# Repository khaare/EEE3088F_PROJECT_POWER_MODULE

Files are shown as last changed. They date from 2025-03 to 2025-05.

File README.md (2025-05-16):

# EEE3088F_PROJECT_POWER_MODULE
The project involves designing and manufacturing the Micromouse(MM) power module.
This repo has two more branches. One for Khaarendiwe and the other for Joshua.
These branches were separated because we worked on different parts of the design, focusing on
different requirements and specifications.

The final design schematic and PCB are under the Main PCB folder, and the folder submitted for manufacturing is the Submission #1 folder

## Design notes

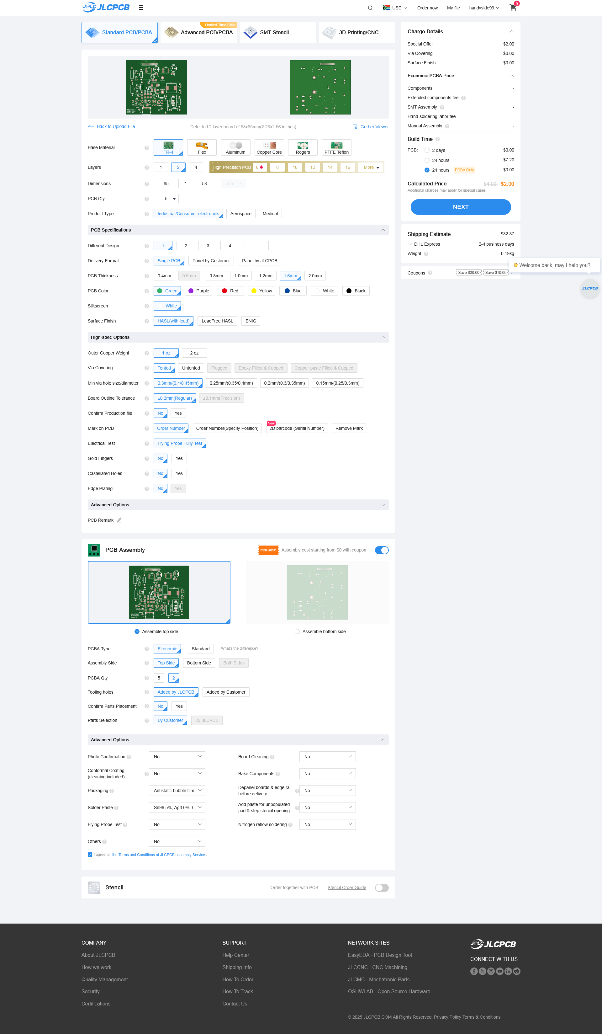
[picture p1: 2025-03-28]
Submission #1/EEE3088F 2025 Project PCB Files Group 46 HNDJOS012 MLDKHA010/EEE3088F_Project_JLCPCBacceptance_HNDJOS012.png

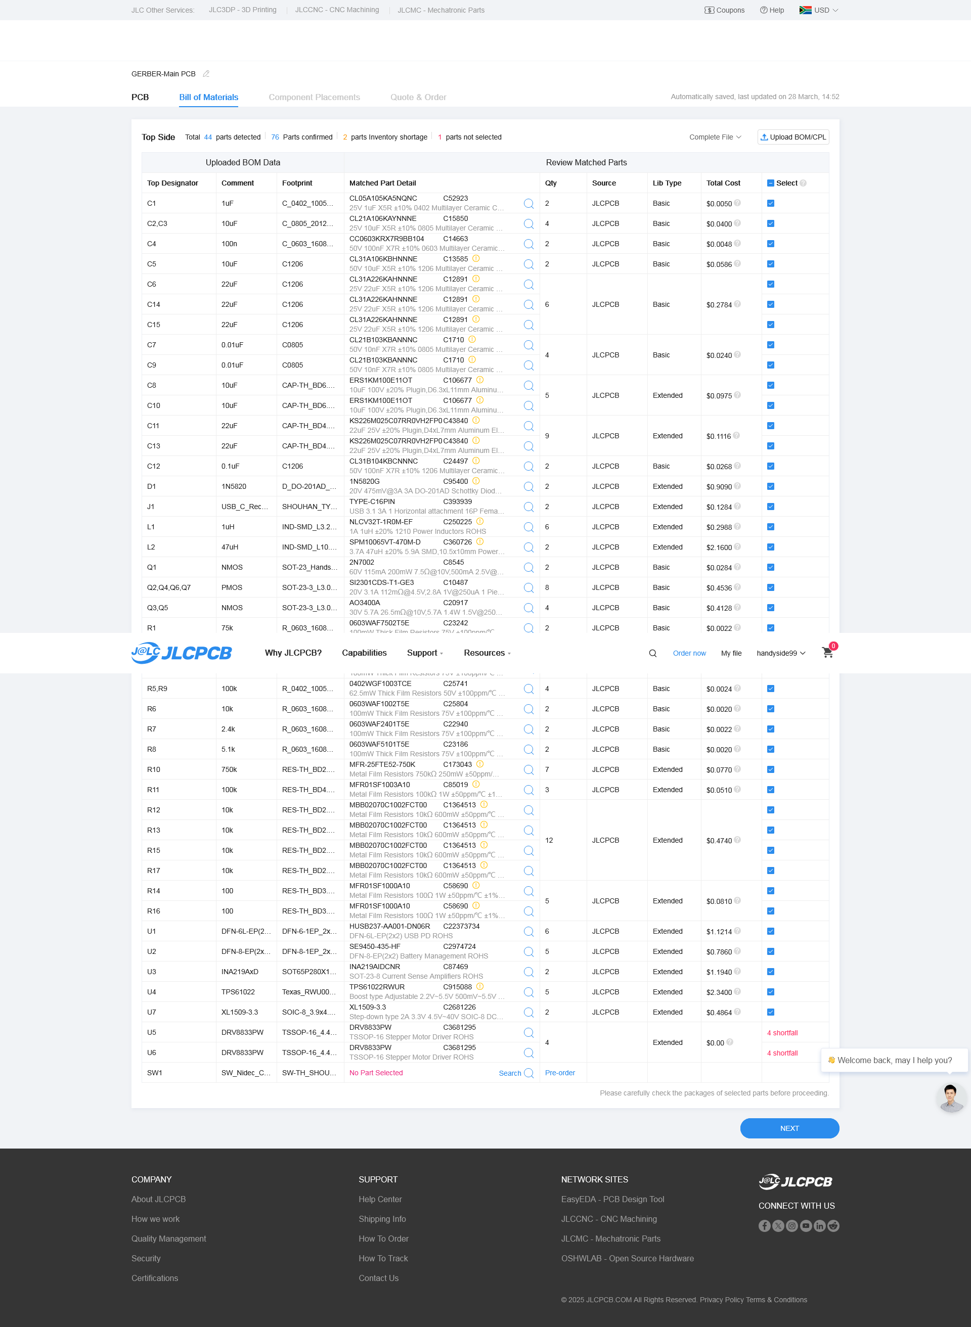
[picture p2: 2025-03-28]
Submission #1/EEE3088F 2025 Project PCB Files Group 46 HNDJOS012 MLDKHA010/EEE3088F_Project_JLCPCBBOM_HNDJOS012.png

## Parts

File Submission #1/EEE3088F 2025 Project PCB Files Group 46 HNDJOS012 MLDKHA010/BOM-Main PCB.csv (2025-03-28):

Comment | Designator | Footprint | LCSC | Quantity
PMOS | Q2,Q4,Q6,Q7 | SOT-23-3_L3.0-W1.7-P0.95-LS2.9-BR | C10487 | 4
100n | C4 | C_0603_1608Metric_Pad1.08x0.95mm_HandSolder | C14663 | 1
10uF | C2,C3 | C_0805_2012Metric_Pad1.18x1.45mm_HandSolder | C15850 | 2
NMOS | Q3,Q5 | SOT-23-3_L3.0-W1.7-P0.95-LS2.9-BR | C20917 | 2
DFN-6L-EP(2x2)_USB_PD_ROHS | U1 | DFN-6-1EP_2x2mm_P0.65mm_EP1x1.6mm | C22373734 | 1
2.4k | R7 | R_0603_1608Metric_Pad0.98x0.95mm_HandSolder | C22940 | 1
3.3k | R4 | R_0603_1608Metric_Pad0.98x0.95mm_HandSolder | C22978 | 1
5.1k | R8 | R_0603_1608Metric_Pad0.98x0.95mm_HandSolder | C23186 | 1
75k | R1 | R_0603_1608Metric_Pad0.98x0.95mm_HandSolder | C23242 | 1
100m | R2,R3 | R_1206_3216Metric_Pad1.30x1.75mm_HandSolder | C25334 | 2
100k | R5,R9 | R_0402_1005Metric_Pad0.72x0.64mm_HandSolder | C25741 | 2
10k | R6 | R_0603_1608Metric_Pad0.98x0.95mm_HandSolder | C25804 | 1
DFN-8-EP(2x2) Battery Management ROHS | U2 | DFN-8-1EP_2x2mm_P0.5mm_EP1.05x1.75mm | C2974724 | 1
USB_C_Receptacle_USB2.0_16P | J1 | SHOUHAN_TYPE-C_16PIN_2MD__073_ | C393939 | 1
1uF | C1 | C_0402_1005Metric_Pad0.74x0.62mm_HandSolder | C52923 | 1
NMOS | Q1 | SOT-23_Handsoldering | C8545 | 1
INA219AxD | U3 | SOT65P280X145-8N | C87469 | 1
0.01uF | C7 | C0805 |  | 1
SW_Nidec_CAS-120A1 | SW1 | SW-TH_SHOU-HAN_SS12D10G4 |  | 1
XL1509-3.3 | U7 | SOIC-8_3.9x4.9mm_P1.27mm |  | 1
22uF | C14 | C1206 |  | 1
TPS61022 | U4 | Texas_RWU0007A_VQFN-7_2x2mm_P0.5mm |  | 1
Conn_01x02_Pin | J3 | PinHeader_1x02_P1.00mm_Vertical |  | 1
10uF | C10 | CAP-TH_BD6.3-P2.50-D1.0-FD |  | 1
22uF | C13 | CAP-TH_BD4.0-P1.50-D0.8-FD |  | 1
22uF | C6 | C1206 |  | 1
1uH | L1 | IND-SMD_L3.2-W2.5_L3225 |  | 1
100k | R11 | RES-TH_BD4.0-L11.5-P15.50-D0.7 |  | 1
Conn_02x16_Odd_Even | J2 | PinHeader_2x16_P1.00mm_Vertical |  | 1
10uF | C5 | C1206 |  | 1
10k | R17 | RES-TH_BD2.5-L6.5-P10.50-D0.6 |  | 1
22uF | C11 | CAP-TH_BD4.0-P1.50-D0.8-FD |  | 1
100 | R14 | RES-TH_BD3.3-L9.0-P13.00-D0.6 |  | 1
DRV8833PW | U5 | TSSOP-16_4.4x5mm_P0.65mm |  | 1
DRV8833PW | U6 | TSSOP-16_4.4x5mm_P0.65mm |  | 1
0.1uF | C12 | C1206 |  | 1
10k | R12 | RES-TH_BD2.5-L6.5-P10.50-D0.6 |  | 1
47uH | L2 | IND-SMD_L10.5-W10.0 |  | 1
100 | R16 | RES-TH_BD3.3-L9.0-P13.00-D0.6 |  | 1
10uF | C8 | CAP-TH_BD6.3-P2.50-D1.0-FD |  | 1
750k | R10 | RES-TH_BD2.4-L6.3-P10.30-D0.6 |  | 1
0.01uF | C9 | C0805 |  | 1
10k | R15 | RES-TH_BD2.5-L6.5-P10.50-D0.6 |  | 1
10k | R13 | RES-TH_BD2.5-L6.5-P10.50-D0.6 |  | 1
1N5820 | D1 | D_DO-201AD_P15.24mm_Horizontal |  | 1
22uF | C15 | C1206 |  | 1

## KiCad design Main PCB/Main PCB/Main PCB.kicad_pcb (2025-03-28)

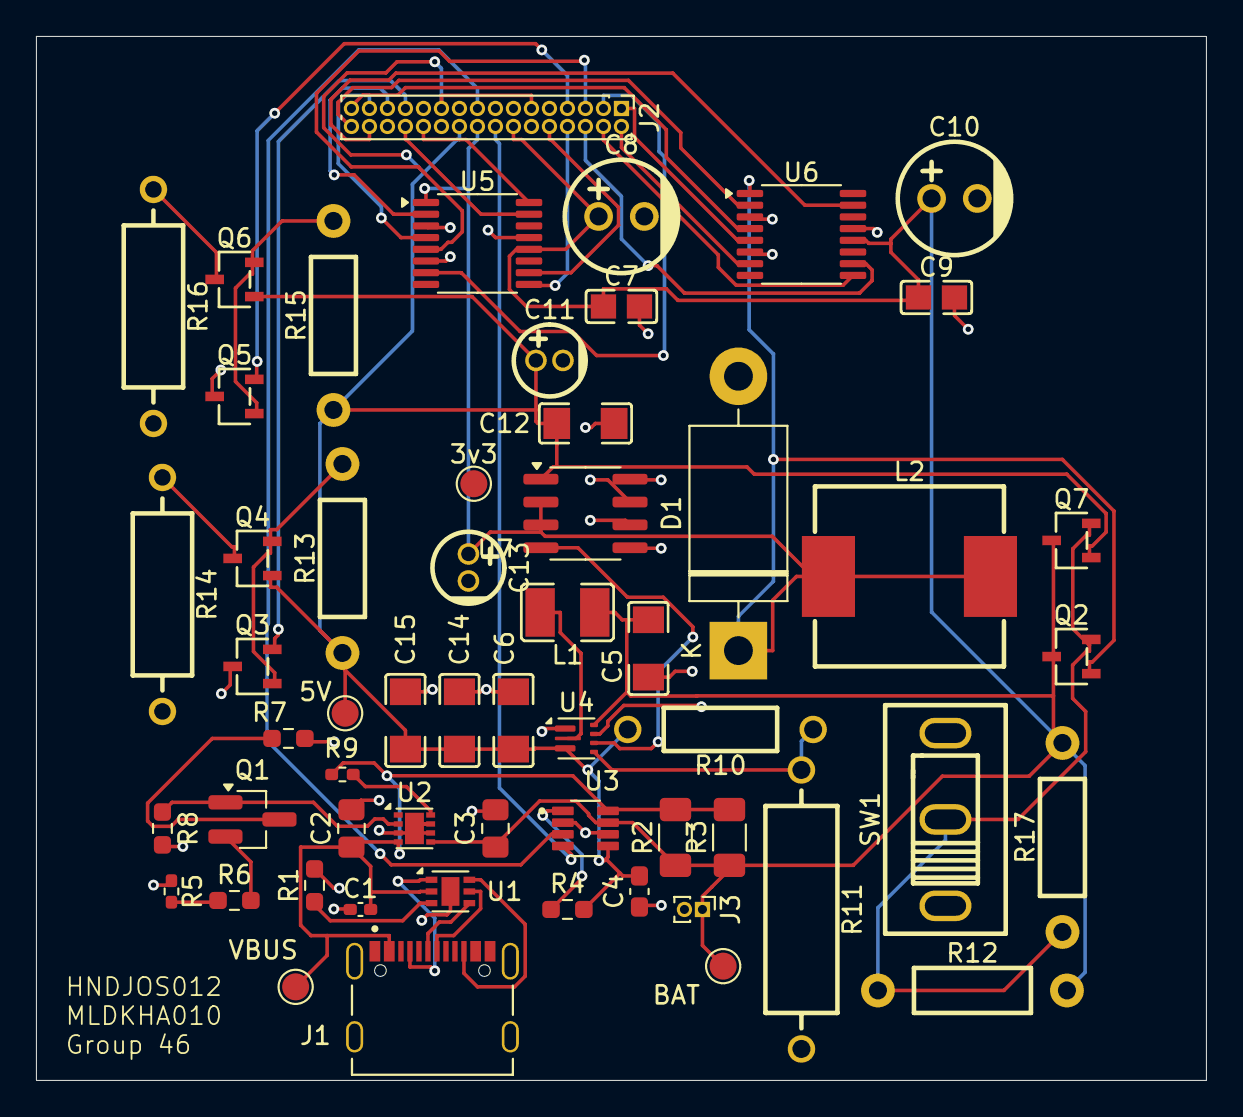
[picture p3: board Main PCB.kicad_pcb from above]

Board: 2 copper layers, 65.0 x 58.0 mm, 57 parts (0 on the bottom side), 43 nets.

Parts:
3v3, 5V: TestPoint_Pad_D1.5mm
BAT: TestPoint_Pad_D1.5mm
C1: 1uF; C_0402_1005Metric_Pad0.74x0.62mm_HandSolder
C2, C3: 10uF; C_0805_2012Metric_Pad1.18x1.45mm_HandSolder
C4: 100n; C_0603_1608Metric_Pad1.08x0.95mm_HandSolder
C5: 10uF; C1206
C6, C14, C15: 22uF; C1206
C7, C9: 0.01uF; C0805
C8, C10: 10uF; CAP-TH_BD6.3-P2.50-D1.0-FD
C11, C13: 22uF; CAP-TH_BD4.0-P1.50-D0.8-FD
C12: 0.1uF; C1206
D1: 1N5820; D_DO-201AD_P15.24mm_Horizontal
J1: USB_C_Receptacle_USB2.0_16P; SHOUHAN_TYPE-C_16PIN_2MD__073_
J2: Conn_02x16_Odd_Even; PinHeader_2x16_P1.00mm_Vertical
J3: Conn_01x02_Pin; PinHeader_1x02_P1.00mm_Vertical
L1: 1uH; IND-SMD_L3.2-W2.5_L3225
L2: 47uH; IND-SMD_L10.5-W10.0
Q1: NMOS; SOT-23_Handsoldering
Q2, Q4, Q6, Q7: PMOS; SOT-23-3_L3.0-W1.7-P0.95-LS2.9-BR
Q3, Q5: NMOS; SOT-23-3_L3.0-W1.7-P0.95-LS2.9-BR
R1: 75k; R_0603_1608Metric_Pad0.98x0.95mm_HandSolder
R2, R3: 100m; R_1206_3216Metric_Pad1.30x1.75mm_HandSolder
R4: 3.3k; R_0603_1608Metric_Pad0.98x0.95mm_HandSolder
R5, R9: 100k; R_0402_1005Metric_Pad0.72x0.64mm_HandSolder
R6: 10k; R_0603_1608Metric_Pad0.98x0.95mm_HandSolder
R7: 2.4k; R_0603_1608Metric_Pad0.98x0.95mm_HandSolder
R8: 5.1k; R_0603_1608Metric_Pad0.98x0.95mm_HandSolder
R10: 750k; RES-TH_BD2.4-L6.3-P10.30-D0.6
R11: 100k; RES-TH_BD4.0-L11.5-P15.50-D0.7
R12, R13, R15, R17: 10k; RES-TH_BD2.5-L6.5-P10.50-D0.6
R14, R16: 100; RES-TH_BD3.3-L9.0-P13.00-D0.6
SW1: SW_Nidec_CAS-120A1; SW-TH_SHOU-HAN_SS12D10G4
U1: DFN-6L-EP(2x2)_USB_PD_ROHS; DFN-6-1EP_2x2mm_P0.65mm_EP1x1.6mm
U2: DFN-8-EP(2x2) Battery Management ROHS; DFN-8-1EP_2x2mm_P0.5mm_EP1.05x1.75mm
U3: INA219AxD; SOT65P280X145-8N
U4: TPS61022; Texas_RWU0007A_VQFN-7_2x2mm_P0.5mm
U5, U6: DRV8833PW; TSSOP-16_4.4x5mm_P0.65mm
U7: XL1509-3.3; SOIC-8_3.9x4.9mm_P1.27mm
VBUS: TestPoint_Pad_D1.5mm

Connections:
/3v3: 3v3.1, C13.1, D1.1 (K), J2.18, L2.1, L2.2, Q2.1 (D), U5.1 (~SLEEP), U6.1 (~SLEEP), U7.2 (OUT), U7.3 (FB)
/5V: 5V.1, C4.2, C6.1, C11.1, C12.1, C14.1, C15.1, J2.11, J2.20, J2.21, Q4.1 (D), Q6.1 (D), Q7.1 (D), R4.2, R10.1, R13.1, R15.1, U3.5 (VS), U4.3 (VOUT), U7.1 (VIN)
/BAT: BAT.1, C3.1, C5.1, C7.1, C8.1, C9.1, C10.1, J2.14, J3.1, L1.1, Q2.3 (S), Q7.3 (S), R2.1, R3.1, R12.2, R17.2, U2.5 (BAT), U3.7 (IN-), U4.7 (VIN), U5.12 (VM), U6.12 (VM)
/CC1: J1.A5 (CC1), U1.1 (CC1)
/CC2: J1.B5 (CC2), U1.6 (CC2)
/D+: J1.A6 (D+), U1.4 (D+)
/D-: J1.A7 (D-), U1.5 (D-)
/Pin 1: J2.1, U6.5 (BOUT2)
/Pin 2: J2.2, U6.7 (BOUT1)
/Pin 3: J2.3, U5.7 (BOUT1)
/Pin 4: J2.4, U6.9 (BIN1)
/Pin 5: J2.5, U5.5 (BOUT2)
/Pin 6: J2.6, U6.10 (BIN2)
/Pin 7: J2.7, Q5.2 (G)
/Pin 8: J2.8, U5.9 (BIN1)
/Pin 10: J2.10, U5.10 (BIN2)
/Pin 13: R5.2, R6.1
/Pin 16: J2.16, U3.4 (SCL)
/Pin 17: J2.17, U3.3 (SDA)
/Pin 24: J2.24, U5.16 (AIN1)
/Pin 25: J2.25, Q3.2 (G)
/Pin 26: J2.26, U5.15 (AIN2)
/Pin 27: J2.27, U5.2 (AOUT1)
/Pin 29: J2.29, U5.4 (AOUT2)
/Pin 30: J2.30, U6.15 (AIN2)
/Pin 31: J2.31, U6.4 (AOUT2)
/Pin 32: J2.32, U6.2 (AOUT1)
/SWITCH_OUT: U4.5 (EN), U7.4 (~EN)
/VBUS: C1.2, C2.1, R2.2, R3.2, R9.1, U1.2 (VBUS), U2.4 (VCC), U3.8 (IN+), VBUS.1
GND: C1.1, C2.2, C3.2, C4.1, C5.2, C6.2, C7.2, C8.2, C9.2, C10.2, C11.2, C12.2, C13.2, C14.2, C15.2, D1.2 (A), J2.19, J2.23, J3.2, Q3.3 (S), Q5.3 (S), R1.2, R5.1, R7.2, R8.2, R11.2, R14.2, R16.2, SW1.1 (C), U1.7 (GND), U2.1 (TS), U2.3 (GND), U2.6 (STBY), U2.7 (CHRG), U2.9 (EP), U3.2 (A0), U3.6 (GND), U4.1 (GND), U4.6 (MODE), U5.3 (AISEN), U5.6 (BISEN), U5.13 (GND), U6.3 (AISEN), U6.6 (BISEN), U6.13 (GND), U7.5 (GND), U7.6 (GND), U7.7 (GND), U7.8 (GND)
unnamed: Q1.1 (D), R8.1, U2.2 (PROG)
unnamed: Q1.2 (G), R6.2
unnamed: Q1.3 (S), R7.1
unnamed: Q2.2 (G), Q7.2 (G), R12.1, R17.1, SW1.2 (B)
unnamed: Q3.1 (D), Q4.2 (G), R13.2
unnamed: Q4.3 (S), R14.1
unnamed: Q5.1 (D), Q6.2 (G), R15.2
unnamed: Q6.3 (S), R16.1
unnamed: R1.1, U1.3 (VSET)
unnamed: R9.2, U2.8 (CE)
unnamed: R4.1, U3.1 (A1)
unnamed: R10.2, R11.1, U4.4 (FB)
unnamed: L1.2, U4.2 (SW)

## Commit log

2025-03-21 Added Schematic and PCB Files
    [CPL-USB-C Integration.csv, USB-C Integration-CuBottom.gbr, USB-C Integration-CuTop.gbr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]
2025-03-21 Updated Charging and Charge Mode Design Documents
    [BOM-USB-C Integration.csv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]
2025-03-22 Req 3 & 4 Circuit Created
    Merged requirements 3 and 4, updated design documents, and created KiCad circuit.
    [9V Charge.kicad_pcb, 9V Charge.kicad_sch]
2025-03-24 Added Component Part Numbers
    [9V Charge.kicad_sch]
2025-03-25 Created INA219 Schematic and PCB
    [INA219 Battery Monitor.kicad_pcb, INA219 Battery Monitor.kicad_sch]
2025-03-25 Update Footprints
    [USB-C Integration.kicad_pcb, USB-C Integration.kicad_sch]
2025-03-26 Updated Footprints
    [USB-C Integration.kicad_pcb]
2025-03-26 Moved Files and Created Main PCB Project
    [9V Charge.kicad_pcb, 9V Charge.kicad_sch, BOM-USB-C Integration.csv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]
2025-03-26 Updated Footprints and Added Joshua's Requirements to Main PCB
    [BOM-Main PCB.csv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]
2025-03-26 Updated Main PCB
    [Main PCB.kicad_pcb]
2025-03-27 Updated Pin Connections
    [Main PCB.kicad_sch]
2025-03-27 Created Main PCB First Draft
    [Main PCB.kicad_pcb, Main PCB.kicad_sch]
2025-03-28 Finalized Main PCB and Generated Gerbers
    [BOM-Main PCB.csv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]
2025-03-28 Updated Footprints and Added First Submission Files
    [BOM-Main PCB.csv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]
